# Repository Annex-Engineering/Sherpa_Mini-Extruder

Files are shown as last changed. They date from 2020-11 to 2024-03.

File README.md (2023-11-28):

## Sherpa Mini - Release 2:

This release adds support for Bondtech's RIDGA v2 in addition to numerous tweaks and updates to make the extruder easier to work on and more reliable than ever. 

## Changelog

+ Bondtech RIDGA v2 compatibility (R2 RC1 and newer)
+ Bondtech insert support
+ Stronger and stiffer idler arm
+ Increased clearance between idler arm and core
+ Minor fixes and adjustments in preparation for upcoming upgrades

+ Core housing and rear housing need to be reprinted if upgrading from Release 1
+ Updated idler arms are backwards compatible with Release 1 and Release 2 RC1

## FAQ
For Material Requirements, Print Settings and How to Interpret the file naming structure, please see: "Print_Settings_and_File_Key.txt"

The BOM and Sourcing Guide for this product can be found here: https://docs.google.com/spreadsheets/d/1O3eyVuQ6M4F03MJSDs4Z71_XyNjXL5HFTZr1jsaAtRc/edit?usp=sharing

## Product Info
This is the Sherpa Mini Extruder, a ground up design developed by Anlin and the team at Annex Engineering. It's a dual geared hobbed filament extruder designed for use with any printer. It features a gear driven design to provide torque while being able to be near silent. You must perform your own tuning to get the best results.

A Pinion Equipped Pancake Stepper is required for this Release.

Our discord server can be found here: 

Join me on Discord (https://discord.gg/MzTR3zE)

Please only use GitHub Issues for repo and file related problems. For general design related questions and technical support please visit our Discord server.

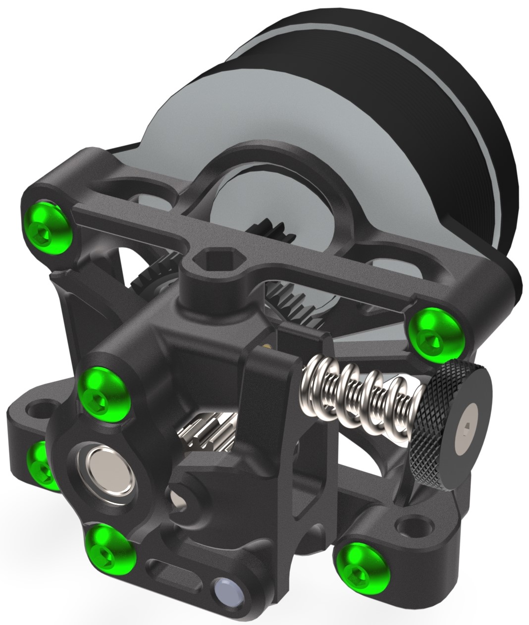
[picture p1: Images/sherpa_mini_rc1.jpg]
Image of Sherpa Extruder


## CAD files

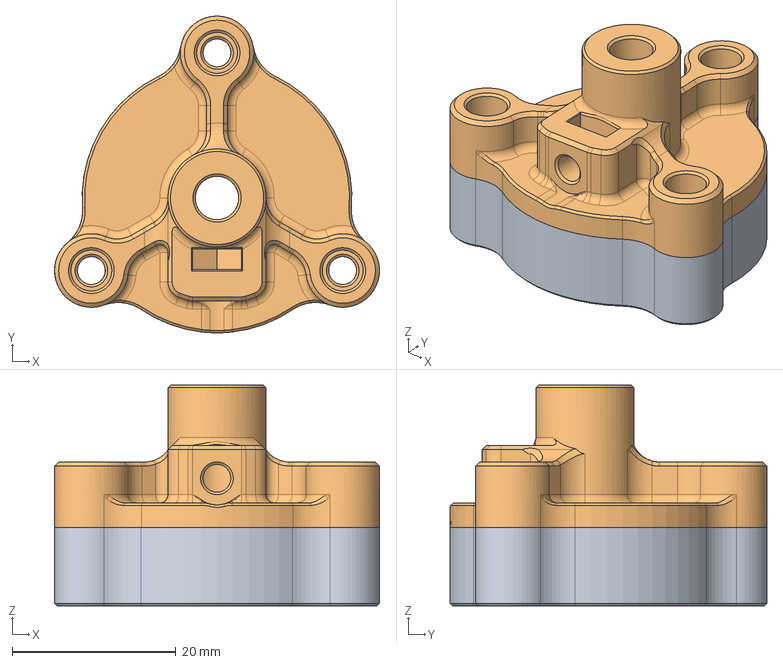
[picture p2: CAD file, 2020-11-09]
Assembly_Tools/Shaft_Grinding_Tool/shaft_block v4.step
39.8 x 38.8 x 27.0 mm
bottom
top

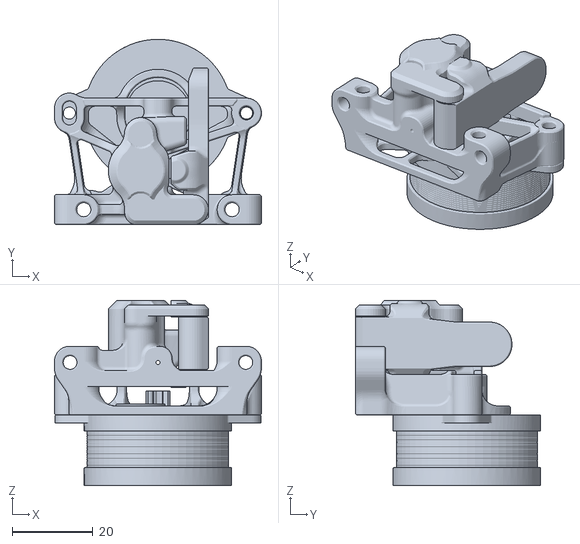
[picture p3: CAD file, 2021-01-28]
Mockup_CAD/sherpa_mini_b3_mockup.STL
51.2 x 45.9 x 45.9

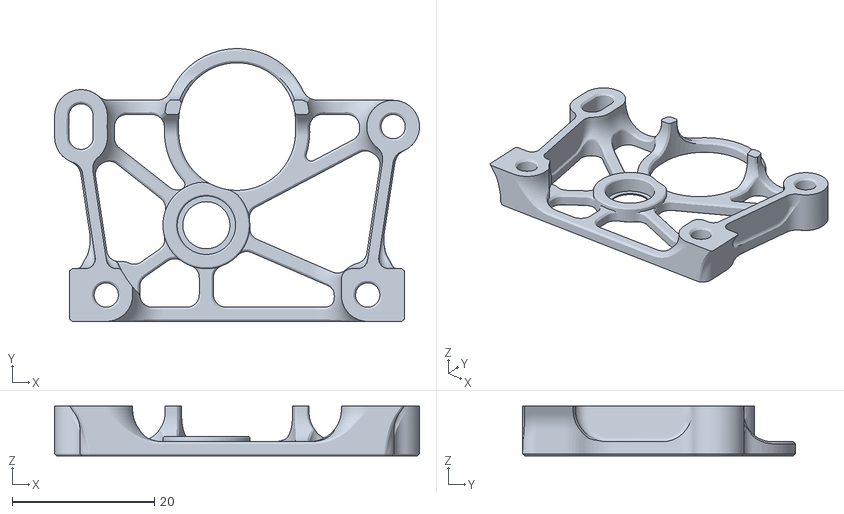
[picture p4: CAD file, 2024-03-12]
STLs/housing_rear_x1_rev17.STL
51.2 x 38.3 x 7.00

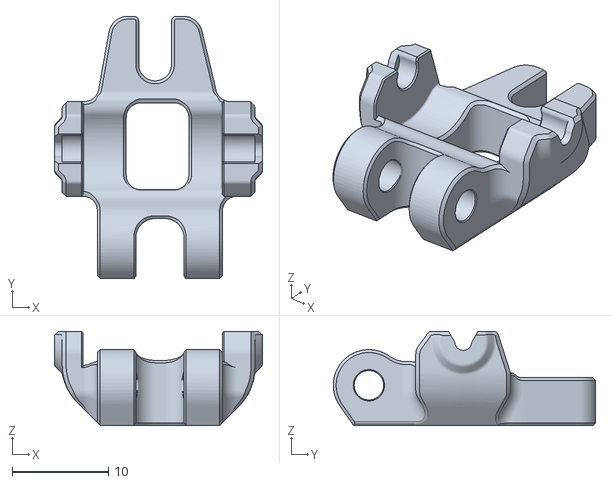
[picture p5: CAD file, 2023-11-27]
STLs/optional_parts/[a]_idler_arm_short_x1_rev16a.STL
21.6 x 27.3 x 9.80

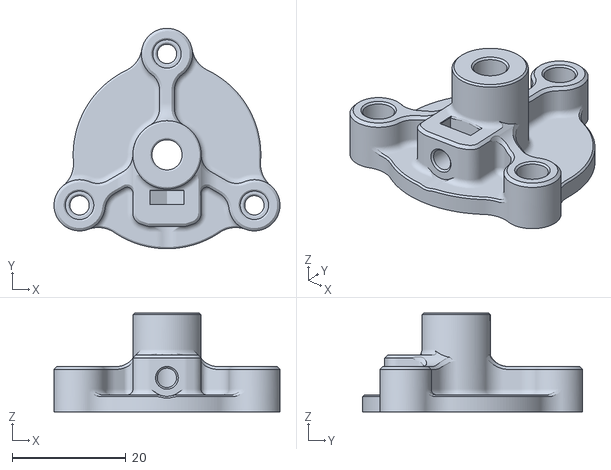
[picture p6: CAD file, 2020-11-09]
Assembly_Tools/Shaft_Grinding_Tool/top.stl
39.7 x 38.8 x 17.4

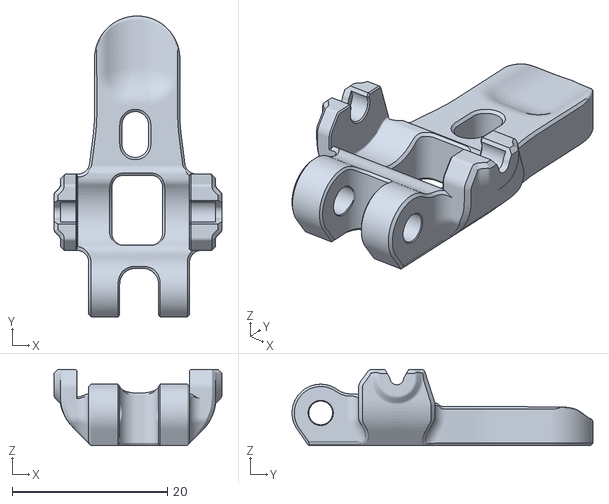
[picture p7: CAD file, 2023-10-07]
STLs/[a]_idler_arm_long_x1_rev16a.STL
21.6 x 38.8 x 9.80

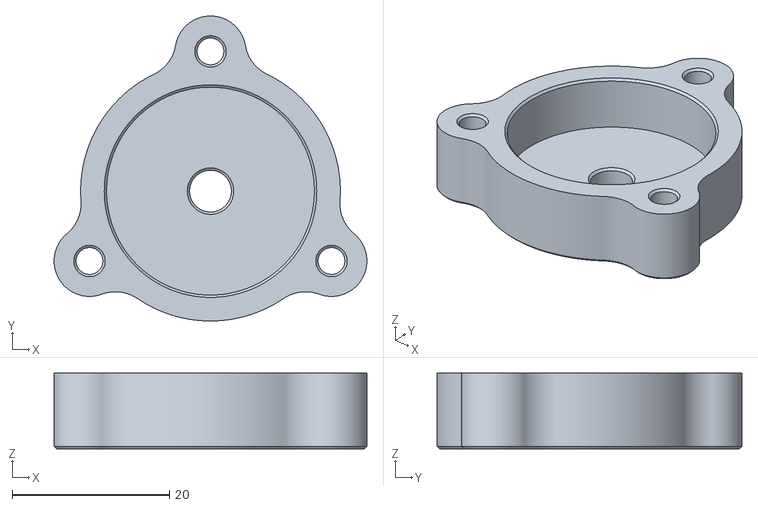
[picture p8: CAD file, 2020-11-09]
Assembly_Tools/Shaft_Grinding_Tool/bottom.stl
39.7 x 38.7 x 9.60

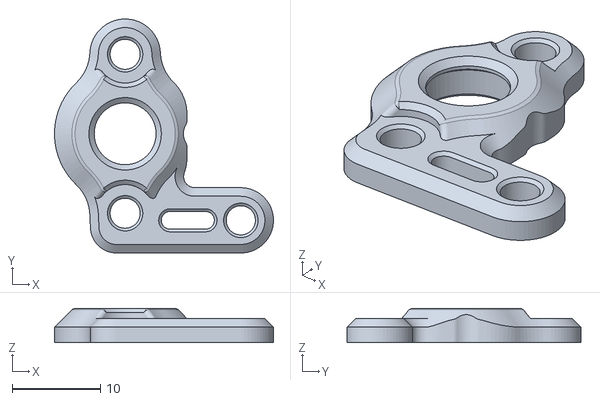
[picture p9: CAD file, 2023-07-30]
STLs/[a]_housing_front_x1_rev15.STL
24.8 x 26.5 x 3.90

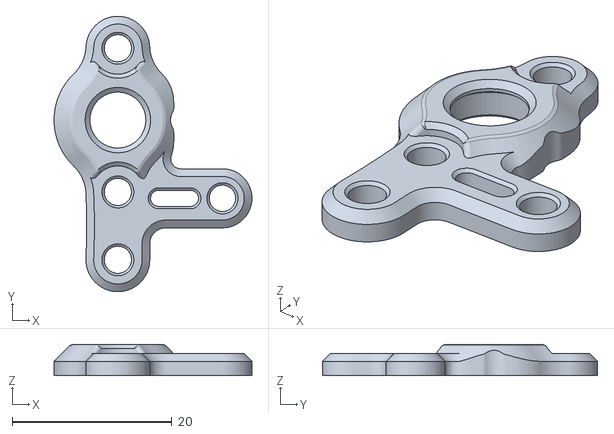
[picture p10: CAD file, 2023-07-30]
STLs/optional_parts/[a]_housing_front_k_x1_rev15.STL
24.8 x 34.5 x 3.90

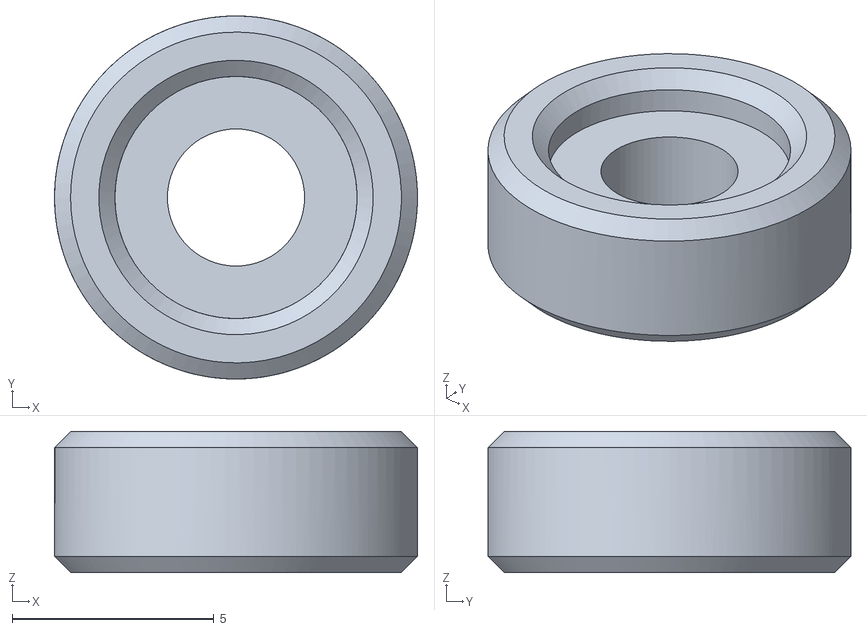
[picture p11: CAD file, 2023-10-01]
STLs/optional_parts/[a]_bondtech_thumbscrew_spacer_x1_rev1.STL
9.00 x 9.00 x 3.50

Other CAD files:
Mockup_CAD/sherpa_mini_b3_mockup.x_t

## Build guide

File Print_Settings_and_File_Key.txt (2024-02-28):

Primary Color: nothing at start of file name
Accent Color: [a]_ at start of file name
Quantity Required: _x# near end of file name
File Revision: _Rev# at end of file name

Nozzle Size: 0.4mm (RECOMMENDED)
Recommended FDM Materials: ASA (Fillamentum, Prusament, Polymaker or 3DXTech Recommended)
Alternate Approved FDM Materials: PC (3DXTech Recommended)
Layer Height: 0.10mm or 0.2mm
Extrusion Width: Forced 0.4mm
Infill Percentage: 40% minimum (at 0.6mm Width)
Infill Type: Grid, Gyroid, Honeycomb, Triangle or Cubic
Wall Count: 4 minimum (at 0.4mm Width)
Solid Top/Bottom Layers: 5 minimum (at 0.2mm Height)

Nozzle Size: 0.5mm 
Recommended FDM Materials: ASA (Fillamentum, Prusament, Polymaker or 3DXTech Recommended)
Alternate Approved FDM Materials: PC (3DXTech Recommended)
Layer Height: 0.1 or 0.2mm
Extrusion Width: Forced 0.5mm
Infill Percentage: 40% minimum (at 0.6mm Width)
Infill Type: Grid, Gyroid, Honeycomb, Triangle or Cubic
Wall Count: 4 minimum (at 0.5mm Width)
Solid Top/Bottom Layers: 5 minimum (at 0.2mm Height)

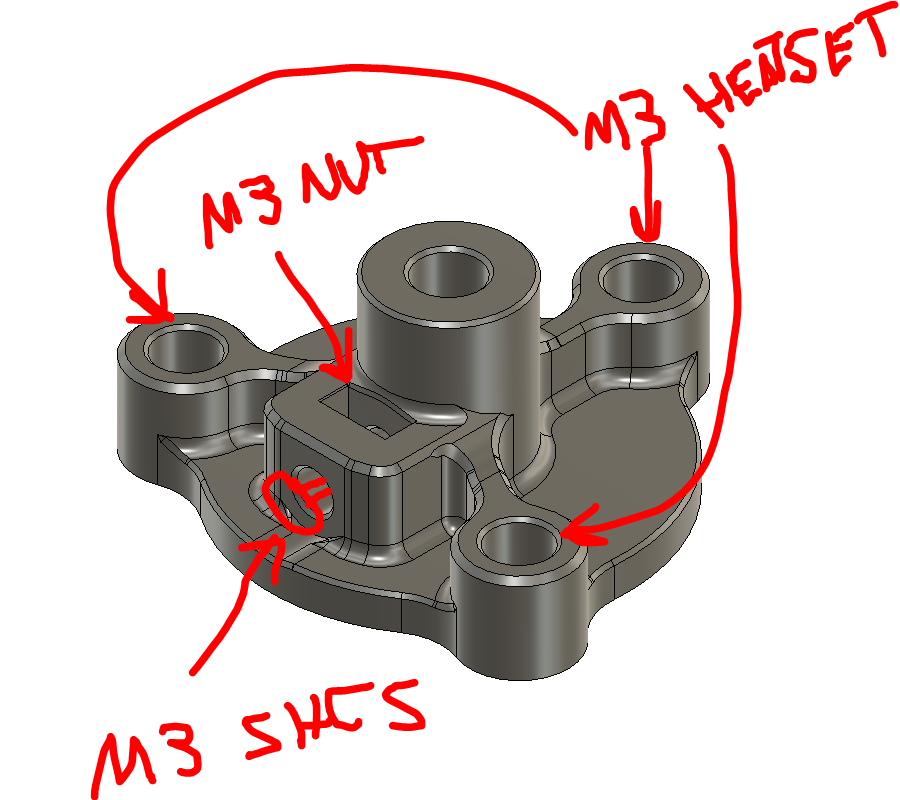
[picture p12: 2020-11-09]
Assembly_Tools/Shaft_Grinding_Tool/tool_2.png

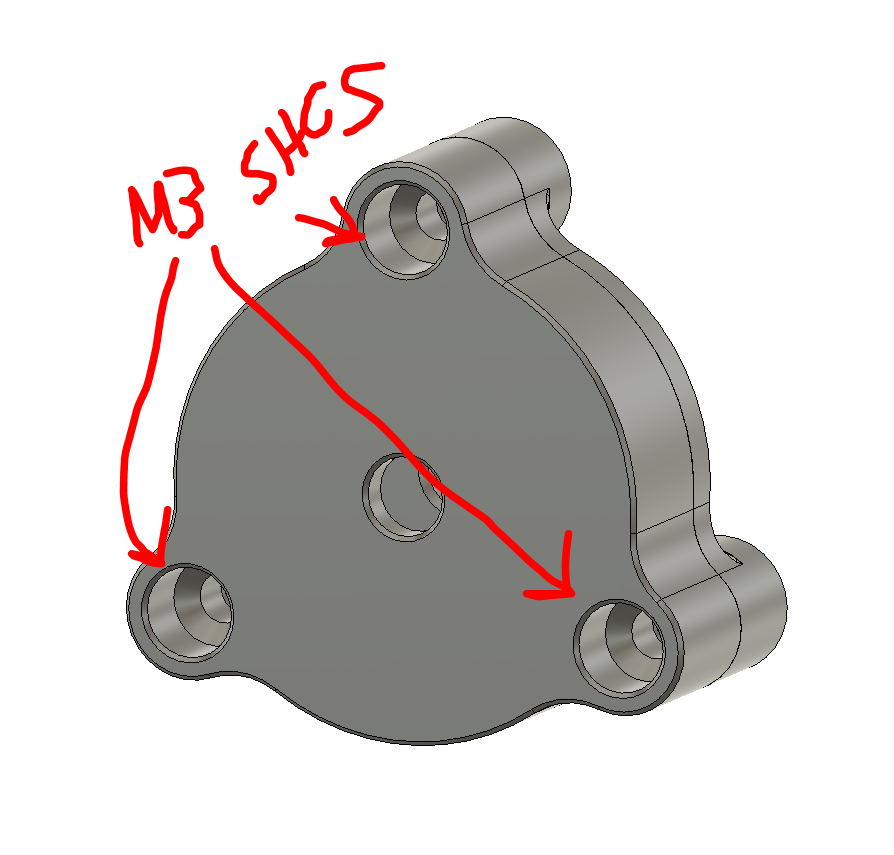
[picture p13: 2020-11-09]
Assembly_Tools/Shaft_Grinding_Tool/tool_1.png

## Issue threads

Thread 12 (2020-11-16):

Step file release.

ChipCE, 2020-11-16:
Hello, thank for very nice design!
Can you guys please release the CAD or STEP file? I need to modify the extruder to use smaller brass Knurled insert.

Annex-Engineering, 2020-11-16:
Steps are only released with non-beta or non-alpha releases.

Closed 2020-11-16.

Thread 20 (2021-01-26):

Holes for mockup

ssavickiy, 2021-01-26:
Hello. I am developing a direct extruder on UltiSteel, but a new mockup cad rc1/beta3 without a pair of lower tightening holes for the screws. My design implies mounting through them on the hotend. These holes will remain in the new release of the stl? And is it possible to add them for mockup cad ?
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

Annex-Engineering, 2021-01-28:
[https://github.com/Annex-Engineering/Sherpa_Mini-Extruder/commit/74c01825e37052597802892bef388b0dc6423901](url)

Closed 2021-01-28.

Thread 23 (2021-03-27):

Teflon tube attachement

Lefuneste83, 2021-03-27:
Hi there. I have been using the Sherpa Mini on my Voron V0 and it is a great design. The only issue I have (and it is a constant pain) is that the bowden tube does not hold in place in the hexagonal hole at the top of the extruder. There is no way I could use glue on a teflon tube. It would not hold to the material. Have you considered a slight modification of this hole to allow for a bowden adapter such as a PC4-M5 or a small clip version. I will try to drill out this hex hole to fit such an adapter but it would be great to provision something for it in the base design.

ChipCE, 2021-03-27:
I agree with @Lefuneste83. Or provide the cad file,it's very hard to deal with the stl with too many curve corners. I can only modify the file in tinkle cad, other softwares I tried failed to map the faces into solid object.

szaghi, 2021-03-27:
Hi all, I have just worked at simple mod using a collet to retain the PTFE tube at the top of the extruder, it is really wip, some modifications are needed (the collet hole is too much small, the collet is too much tight in the current version), I hope to fix it soon, but I can share my simple mod if someone is interested (see pictures attached). It is only a temporary mod until an "official" version with integrated PTFE connector will be available.

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

szaghi, 2021-03-28:
Hi all,

I have fixed some tolerances of my stupid collet-mod, I attach this version below.

Cheers

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
[sherpa-collet-ptfe.zip](https://github.com/Annex-Engineering/Sherpa_Mini-Extruder/files/6217217/sherpa-collet-ptfe.zip)

Annex-Engineering, 2021-03-28:
You guys are welcome to put in a pull request for a user mod. There's a folder on the top level of the directory for this.

Annex-Engineering, 2021-03-30:
user mod has been  added, closing issue

szaghi, 2021-03-30:
Hi all,

I have just created a PR (https://github.com/Annex-Engineering/Sherpa_Mini-Extruder/pull/24) with a *user mod* to provide a version of the housing core with an integrated PTFE retaining collet (see the picture below).

Cheers

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

drewgwallace, 2024-05-12:
I am not finding this adaptation for a PTFE retainer in the user mods - was it removed?

https://github.com/Annex-Engineering/Annex-Engineering_User_Mods/tree/main/Extruders/Sherpa_Mini/Extruder_Mods

Closed 2021-03-30.

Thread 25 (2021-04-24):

collet adapter version has too large hole

5PAZT1C, 2021-04-24:
the hole for the collet adapter as measured is 6.5-6.7mm, for proper fitment with e3d collets the hole needs to be 6mm.

Were the CAD for the modifed version provided, it would be a very easy fix, however the user mod version has no CAD file posted.

5PAZT1C, 2021-04-24:
to further expand on the issue, I have one collet that 'fits' however it is very easy to pop out and the raised lip is also too short, so that even with the retaining clip it wiggles quite a bit. Suggest changing diameter of lip to 6.00mm from it's current ~6.5mm as printed, and increasing the length of the lip by 1.5mm to decrease the amount of play in the collet fitting once retaining clip is inserted.

Alternatively, suggest providing a part number for a collet to be used with this mod, preferably one available from multiple vendors

szaghi, 2021-04-25:
@5PAZT1C

Thank you very much for the insight, I dimensioned the mod with the collet I had (an unknown-manufacturer Chinese one) and with the tolerance of my printer. Now that the CAD file of version 1 has been provided I can re-desing the collet adapter with the dimensions you pointet out. ASAP I will provide the step of my mod with fixed dimensions.

Regards,
Stefano

5PAZT1C, 2021-04-25:
if it helps I found the datasheet for the e3d collet:
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

I would think that making both the inner diameter of the bore and the lip slightly undersized with a taper leading from the inner diameter to the lip would result in a good fitting collet adapter. You can see the documentation for the e3d v6 lite here to see what I mean:

https://wiki.e3d-online.com/images/8/84/DRAWING-LITE6-175-SINK.png

szaghi, 2021-04-25:
@5PAZT1C

This helps a lot, I will use this E3D datasheet as a reference, thank you again.

5PAZT1C, 2021-04-25:
> @5PAZT1C
>
> This helps a lot, I will use this E3D datasheet as a reference, thank you again.

sure thing! Glad I could help contribute, even if it's something small. I'll keep an eye out for the updated version and do a test print, I'll follow up on this once printed

szaghi, 2021-04-25:
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

I hope to find the time tomorrow

5PAZT1C, 2021-04-25:
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

no rush, I have to buy more ABS before I can reprint it anyways lol

Annex-Engineering, 2021-06-19:
seems to be a dead issue, closing for now

szaghi, 2021-06-19:
@Annex-Engineering

Yes, I am sorry, but currently I have not the time to fix it, I hope to find it soon

szaghi, 2021-09-08:
[sherpa-ptfe-collet-retain.zip](https://github.com/Annex-Engineering/Sherpa_Mini-Extruder/files/7131332/sherpa-ptfe-collet-retain.zip)

@5PAZT1C

I am very sorry for my delay, but I was very busy. I have attached a preliminary version of the modified housing with PTFE collet retainer integrated (the whole step and the STL of the modified housing): I designed the collet and housing-collet-retainer using the references you have indicated. Can you give me a feedback (no rush, when you can/want) about it before creating a new PR?

My best regards

5PAZT1C, 2021-09-08:
thanks! I will print it and check fitment when I have time, however it will be quite a while before I can reprint it and check fitment, as I am leaving the country for vacation for a month tommorrow afternoon

szaghi, 2021-09-09:
@5PAZT1C

Do not worry, no rush, enjoy your vacation

Closed 2021-06-19.

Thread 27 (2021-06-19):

VORON0 Retention block missing

mrvanes, 2021-06-19:
The retention block STL is missing in Edward Yeeks VORON0 toolhead.

oldfar-t, 2021-09-08:
It looks like the file was deleted from the v0 Github in april, you can still dig it up through Github search but I've also attached it. It would be nice if it could be put in the STLs folder though.
[[a]_Belt_Retention_Block_x1.zip](https://github.com/Annex-Engineering/Sherpa_Mini-Extruder/files/7125615/a._Belt_Retention_Block_x1.zip)

Closed 2021-09-10.

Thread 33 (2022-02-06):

version with 4.6 inserts

iamkarlson, 2022-02-06:
Is there any technical limitation on why 4.6 mm inserts cannot be used? they seem to be super popular in the Netherlands/Germany and 5mm is almost only can be bought from Chinese shops.

dan-and, 2022-02-08:
Well, there is a 4.6 User-Mod at https://github.com/Annex-Engineering/Sherpa_Mini-Extruder/tree/8163d3f125bbe51e7492368310ab6a8a0761f063/User_Mods which was moved to a new repo with the last commit here.
Maybe check that out or have a look at the sherpa micro project, which may looks like the successor of the sherpa mini.

PapeJelly, 2022-02-24:
Looks like iamkarlson's request has been fulfilled. Therefore i will close this issue.

Closed 2022-02-24.

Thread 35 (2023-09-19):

Wrong STL files?

ogland, 2023-09-19:
I downloaded the latest release files for Sherpa Mini, but what I printed was Sherpa Micro. Are the STLs wrong?

anlin93, 2023-09-24:
Thanks for bringing this to our attention. The issue has now been fixed

Closed 2023-09-24.

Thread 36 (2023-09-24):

Can you make this part more reliable?

pasha4ur, 2023-09-24:
Hello

I printed this part from ABS+ on different printers. It constantly breaks down. I have already replaced 5 parts and 2 sets of gears.

Make it more reliable. Please.

[https://i.ibb.co/XVK9r0Z/photo-2023-09-24-14-00-50.jpg](https://i.ibb.co/XVK9r0Z/photo-2023-09-24-14-00-50.jpg)

anlin93, 2023-09-24:
White ABS is known to be prone to all sorts of problems and is not recommended for structural parts. We very rarely see failures around the idler arm pivot when printed out of ASA (or ABS in almost any other colour). The failure in your case seems to be related to inadequate layer adhesion which can be caused by a number of things, one of them being the material. Overextrusion or badly printed overhangs can also stress the plastic around the pivot, so if the pivot shaft requires more than a firm push against a hard surface to insert, you may need to adjust your print settings and/or ream out the pivot hole. There is not enough detail about the print settings, material or the printer to provide a more comprehensive answer. My suggestion is to try a different material (black ASA preferred) and make sure the print settings are appropriate for the material and your printer. If you require further assistance, feel free to post in #sherpa_help_forum on our Discord server, which is our main support channel.

pasha4ur, 2023-09-24:
I printed it in black too. This is bad design problem.

dan-and, 2023-09-24:
I'm sorry, but I haven't had any problems with the structure. I'm using 5 mini and micros and they never broke. I'm not even using the recommended materials, but an ASA from a spanish manufacturer.

anlin93, 2023-09-24:
Sherpa has been out 3 years and so far there have only been a handful of reports of this issue, basically all of which can be attributed to bad prints. As the problem remains isolated to your case, no design changes are planned. If you want to post your modified file as a mod, feel free to make a pull request. Any further communication should happen on our Discord server, as instructed above. I will add a note to the main repo README that GitHub issues are not a forum for technical support.

Closed 2023-09-24.

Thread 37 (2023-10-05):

Normal cad file

pasha4ur, 2023-10-05:
Hello

Why don't you share stp or other editable file format as Salfin, Orbiter, Vz-HextrudORT, etc?

Edrawings can't be imported in solidworks and other apps. It says about unsupported format.

anlin93, 2023-10-05:
Cad files for the R2 will be released when it reaches final release status. Cad files for R1 are available here: https://github.com/Annex-Engineering/Sherpa_Mini-Extruder/tree/87c5b7f5262ed1ce753bf90fcbf62043f1d25eba/CAD

Closed 2023-10-05.

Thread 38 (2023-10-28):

Sherpa Klipper Config

4e576rt8uh9ij9okp, 2023-10-28:
Hello there, so I have seen links online to this here but sadly someone decided to delete it.
https://github.com/Annex-Engineering/Sherpa_Mini-Extruder/blob/master/Klipper_Config_Block.txt

Now will there be a klipper config for it or does the whole world need to reinvent the wheel (every person needs to find it out)

anlin93, 2023-11-02:
The Klipper config block can be found here:
https://github.com/Annex-Engineering/ANNEX-Printer-Firmware/tree/main/Klipper_and_Klipper_Derivatives/Sherpa_Mini

Closed 2023-11-02.

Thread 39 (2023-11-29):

Little questions about print settings

celtare21, 2023-11-29:
So in the print settings it states as follows:

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

Does that mean that the extrusion width for infill is 0.8 like this?
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

And what does 4 top/bottom laters at 0.5mm **Height** mean more exactly?

Thank you

ChaosBlades, 2024-02-28:
Those settings are for 0.5mm nozzles. Most people have 0.4mm which is after those settings. Don't know why those settings are even listed to be honest. Does not even apply to 99.9% of people. Don't even think that is an exaggeration.

If you have printed Voron parts at Voron recommended settings then you can print this at those same settings. Plenty of guides and information online on how to do that.

celtare21, 2024-02-28:
> Those settings are for 0.5mm nozzles. Most people have 0.4mm which is after those settings. Don't know why those settings are even listed to be honest. Does not even apply to 99.9% of people. Don't even think that is an exaggeration.
>
> If you have printed Voron parts at Voron recommended settings then you can print this at those same settings. Plenty of guides and information online on how to do that.

I actually have a 0.5 mm nozzle 😅.
The bozzle comes standard with 0.5

ChaosBlades, 2024-02-28:
What printer comes standard with 0.5mm? I have literally never heard of anyone using a 0.5mm nozzle. 0.6, 0.8, and even a 1.2mm nozzle but never 0.5mm.

I just looked through every printer profile OrcaSlicer offers and only the Ender 5 Pro and the two VZBots even have profiles for 0.5mm. Which none of those come standard with them.

celtare21, 2024-02-28:
> What printer comes standard with 0.5mm? I have literally never heard of anyone using a 0.5mm nozzle. 0.6, 0.8, and even a 1.2mm nozzle but never 0.5mm.
>
> I just looked through every printer profile OrcaSlicer offers and only the Ender 5 Pro and the two VZBots even have profiles for 0.5mm. Which none of those come standard with them.

None come "standard". I have a fully custom printer, everything was replaced and or modified. I make my own slicer profiles and this is the nozzle I'm using https://northprint3d.ca/product/tungsten-carbide-nozzle-high-flow/

anlin93, 2024-02-28:
Sorry, somehow this issue slipped through the cracks and I only got a notification for it now. The print settings file will probably be removed at some point as the relevant information can be found in the build manual. For now I've updated the print settings file to match our current recommendations.

Closed 2024-02-28.

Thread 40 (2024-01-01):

Release 2 CAD missing idler_arm_long

310weber, 2024-01-01:
The CAD for release 2 seems to be missing the idler_arm_long part (or rather the part shows up in the model tree but is empty).

Steps to reproduce:
1. download parasolid model [sherpa_mini_release_2.x_t](https://github.com/Annex-Engineering/Sherpa_Mini-Extruder/blob/master/CAD/sherpa_mini_release_2.x_t) from commit [fa76f44](https://github.com/Annex-Engineering/Sherpa_Mini-Extruder/commit/fa76f449e86c1e4ee2c25fc557be01597a096812)
2. import model to Onshape
3. navigate to "idler_arm_long^housing_sherpa_mini_a3_r16(FDM)" in the model tree
4. part is empty

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

ChaosBlades, 2024-02-28:
It is not missing... just really really small 🤣 I compared Release 1 and Release 2 arms. The geometry is different so you can't simply split the old thumb lever and add it to the new idler arm short.
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
Also, would be nice when this is fixed it is updated to a Step file instead of the Parasolid file. The ONLY free way a user can use that file is add it to Onshape then export it as a Step. Who knows how long it will be before that is locked behind a pay wall as well.

So people don't have to make an Onshape account to use the current CAD I have already converted it.
[sherpa_mini_release_2.zip](https://github.com/Annex-Engineering/Sherpa_Mini-Extruder/files/14431012/sherpa_mini_release_2.zip)

anlin93, 2024-02-28:
This looks to be an issue related to Onshape. The X_T opens fine in SolidWorks, long idler arm included
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

Closed 2024-02-28.

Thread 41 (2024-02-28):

Release 2 Idler Arm Long collides with idler gear teeth

ChaosBlades, 2024-02-28:
The idler gear teeth hit the long idler arm but not the short. Could be something slightly tweaked on the long version of the arm. Can't tell if there is anything different about them due to https://github.com/Annex-Engineering/Sherpa_Mini-Extruder/issues/40 or if it is a print issue. It does spin free if I put the gear in backwards. The tolerances on both due seem unnecessarily tight or the idler I have just has slightly longer teeth than the one used to design the part.

In CAD the Idler gear is 9.46mm in diameter and mine is 9.54mm and the CAD model gears has 0.25mm of clearance with the arm.

anlin93, 2024-02-28:
Please only use GitHub Issues for repo and file related problems. For general design related questions and technical support please visit our Discord server. That being said both idler arm variants have identical gear clearances, so this is most likely a print issue.

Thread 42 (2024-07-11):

Documentation: Current for LDO Motors and Klipper config

leo-hstone, 2024-07-11:
Hi, first: thanks for the awesome design!

Would it be possible to include the current setting for the motor as well as a starting point for a klipper config in this repo? I would be happy to contribute if guided where to place things.

leo-hstone, 2024-07-11:
Just seen #38 - here is all the information. In this case: please include a link to there in the ReadMe in a highlighted position.

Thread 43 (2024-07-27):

Documentation and/or Assembly Tool: PTFE tube length

wirehead, 2024-07-27:
At least by documenting, potentially by creating an assembly tool cutting jig (there might be one?) can there be documentation for how long the PTFE tube ought to stick into the Sherpa?

I think it's 8mm, but I'm not actually sure.

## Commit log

2020-08-27 sherpa mini stl "pre-release"
    sherpa mini stl "pre-release"
    [1011_china_chain_x_carriage_mount_rev1.stl, 4010_cooling_duct_focussed_left_rev1.stl, 4010_cooling_duct_focussed_right_rev1.stl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]
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2020-08-30 MInor tweaks and updates
    Raise omron probe up for clearance in x carriage, tweaks to focussed cooling duct for better performance. Add igus chain mount.
    [4010_cooling_duct_focussed_left_rev1.stl, 4010_cooling_duct_focussed_left_v2.stl, 4010_cooling_duct_focussed_right_rev1.stl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]
2020-08-31 Multiple updates
    - Tweaked heatset insert hole sizes
    - Add Denali/V1.8 compatible carriage
    - Updated dragon mount with inserts coming in from bottom.
    - Added images and a readme
    [dragon_sherpa_mini_mount_single_unit_rev1.stl, dragon_sherpa_mini_mount_single_unit_rev2.stl, x_carriage_left_mag_microswitch_rev1.stl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]
2020-09-06 Update STLs + config
    [Klipper_Config_Block.txt, [a]_idler_carrier_long_x1_rev1.stl, [a]_idler_carrier_long_x1_rev2.stl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]
2020-09-09 add sherpa mini assembly STL
    [sherpa_mini_assy_a1.stl]
2020-09-11 add edwardyeeks experimental sherpa mini v0 toolhead to the repo
    [cooling_fan_duct_left_v1.stl, cooling_fan_duct_right_v1.stl, dragon_toolhead_left_v1.stl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]
2020-09-11 Fix hole positions in dragon & mosquito toolheads. Updated CAD.
    [dragon_toolhead_left_v1.stl, dragon_toolhead_left_v2.stl, dragon_toolhead_right_v1.stl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]
2020-09-12 Add bridges in cooling fan duct screw holes to avoid printing with supports.
    [cooling_fan_duct_left_v1.stl, cooling_fan_duct_left_v2.stl, cooling_fan_duct_right_v1.stl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]
2020-09-12 Fix weird stl orientation causing non-flat top surfaces.
    [cooling_fan_duct_left_v2.stl, cooling_fan_duct_right_v2.stl]
2020-09-15 Add CAD, update magnetic x carriage stls
    - CAD released for the toolhead and x carriage.
    - magnet holes were adjusted to match current moron magnetic microswitch probe.
    - renamed stls to have revx number.
    [4010_cooling_duct_focussed_left_rev2.stl, 4010_cooling_duct_focussed_left_v2.stl, 4010_cooling_duct_focussed_right_rev2.stl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]
2020-09-20 Updated CAD File
    File was missing omron x-carriage.
2020-09-21 Alpha 2 release
    - Reduce frontage and plastic usage.
    - Better wire routing and more ziptie mounting points.
    - Optimise cooling fan duct to blow closer to nozzle (untested).
    [cooling_fan_duct_focussed_left_a2_v1.stl, cooling_fan_duct_focussed_right_a2_v1.stl, cooling_fan_duct_left_v2.stl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]
2020-10-09 Initial commit of Release 2
    - push cooling blower fans forward by 4mm to allow clearance for V1.8 and V2.4 gantries.
    - move microswitch inwards a little bit for V1.8/Denali x carriage.
    - now only supports 4010 axial fan for hotend
    - now only has the updated focussed cooling duct edition
    [4010_cooling_duct_focussed_left_rev2.stl, 4010_cooling_duct_focussed_left_rev3.stl, 4010_cooling_duct_focussed_right_rev2.stl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]
2020-11-04 add pape toolhead for v6s
    [4010_radial_fanduct_focussed_left.STL, 4010_radial_fanduct_focussed_right.STL, V6_sherpa_mini_mount_back.STL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]
2020-11-08 add xile tiny-m toolhead
    [carriage_left.STL, carriage_right.STL, fanduct_left.STL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]
2020-11-08 add edwardyeeks sherpa mini mosquito parts
    [4010_cooling_duct_focussed_left_rev3.stl, 4010_cooling_duct_focussed_right_rev3.stl, 4010_radial_fanduct_focused_left_rev4.STL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]
2020-11-09 add shaft grinding tool
    [bottom.stl, shaft_block v4.step, top.stl]
2020-11-09 add shaft grind tool assembly photos
    [bottom.stl, shaft_block v4.step, top.stl]
2020-11-09 add printable bondtech 50t gear to repo (optional)
    [printable_sherpa_mini_gear_50t_sl_x1_rev1.stl]
2020-11-30 sherpa mini - beta 2
    [[a]_housing_front_kseries_x1_rev1.STL, [a]_housing_front_x1_rev3.STL, [a]_idler_arm_long_x1_rev3.STL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]
2020-11-30 fix short idler arm, wrong version marked
    [[a]_idler_arm_short_alt_x1_rev3.STL, [a]_idler_arm_short_x1_rev3.STL]
2020-12-02 Sherpa Mini V0 Toolhead Beta 1
    [cooling_fan_duct_focussed_left_a2_v1.stl, cooling_fan_duct_focussed_left_rev1.stl, cooling_fan_duct_focussed_right_a2_v1.stl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]
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2020-12-17 Revert cooling ducts to previous rev
    Rev4 cooling ducts were an error which was actually an older revision. Reverted back to rev3. Readme was also updated. Small folder reorganisation.
    [4010_cooling_duct_focussed_left_rev3.stl, 4010_cooling_duct_focussed_right_rev3.stl, 4010_radial_fanduct_focused_left_rev4.STL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]
2020-12-21 fix print orientation
    [[a]_idler_arm_short_alt_x1_rev3.STL]
2020-12-24 add hartk1213 bowden adapter
    [SherpaBowden.STL, SherpaBowden.step]
2020-12-26 Add support for Voron Legacy
    [Arm_1.STL, Arm_2.STL, Belt_clamp.STL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]
2020-12-30 Add support for V2.4
    [2x Beltclip.STL, Cable chain anchor - Generic.STL, Cable chain anchor - IGUS.STL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]
2021-01-01 Add experimental microprobe dock to V2.4 toolhead
    [Experimental_microprobe_arm_rev1.x_t, Microswitch_dock.STL, Mount.STL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]
2021-01-11 move xy carriages to "other printer mods" repo
    [1011_china_chain_x_carriage_mount_rev1.stl, 2x Beltclip.STL, 4010_cooling_duct_focussed_left_rev3.stl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]
2021-01-23 add rc1/beta3 better mockup cad to repo (stls coming soon), actual cad to come with RC1
    [sherpa_mini_assy_a1.stl, sherpa_mini_b2_bottom_profile.DXF, sherpa_mini_b3_mockup.SLDPRT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]
2021-01-28 add front holes to mockup model
    [sherpa_mini_b3_mockup.SLDPRT, sherpa_mini_b3_mockup.STL, sherpa_mini_b3_mockup.x_t]
2021-02-07 update block to rotation distance
    [Klipper_Config_Block.txt]
2021-02-09 Update left cooling duct
    Slightly optimised duct for more even airflow on the left side
    [cooling_fan_duct_focussed_left_rev1.stl, cooling_fan_duct_focussed_left_rev2.stl]
2021-02-25 add k-series bolt down to mockup
    [sherpa_mini_b3_mockup.SLDPRT]
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2021-03-26 added stls
    added stls for the 4.6mm OD insert
    [housing_front.STL, housing_front_k.STL, housing_rear.STL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]
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2021-03-27 move optional parts to optional parts folder
    [[a]_housing_front_kseries_x1_rev2.STL, [a]_idler_arm_short_x1_rev4.STL, printable_sherpa_mini_gear_50t_sl_x1_rev1.stl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]
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2021-03-30 User Mod: housing with integrated PTFE Collet
    Short description:
    Add a new housing core version with integrated PTFE retaining collet for
    a more simple PTFE tube handling. To work it requires additional
    materials, i.e. an E3D like collet and clip.
    This modification has been made from the revision 4.
    Why:
    Make more simple the handling of PTFE tube at the inlet of the extruder.
    This change addresses the need by:
    Add a new mesh of the housing core part.
    Side effects:
    Nothing, but it has not been tested yet.
    Note:
    A minor typo has been fixed into *User_Mods/Readme.md* file.
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2021-04-15 add 8t block for gear ratio, made standard
    [Klipper_Config_Block.txt]
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2021-04-21 add highly experimental stls for SLS and MJF printing
    this does not mean we support parts printed from sls or MJF, these parts exist so we can work with external vendors, test parts, and get properly fitting components
    [[a]_housing_front_k_x1_rev5.STL, [a]_housing_front_x1_rev5.STL, [a]_idler_arm_long_x1_rev5.STL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]
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2021-09-24 Updated to R1 parts
    Past parts were RC1 and these are currently R1.
    [housing_front.STL, housing_front_k.STL, housing_rear.STL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]
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2023-07-30 add correct stls to repo
    [[a]_housing_front_k_x1_rev15.STL, [a]_housing_front_k_x1_rev7.STL, [a]_housing_front_x1_rev15.STL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]
2023-10-07 fixed export of stl, reprint recommended
    [[a]_idler_arm_long_x1_rev16.STL, [a]_idler_arm_long_x1_rev16a.STL]
2023-10-27 migrate printer, extruder and board configs to an MIT licensed repo
    [Klipper_Config_Block.txt]
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2023-12-02 CAD fix
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2024-02-28 Update Print_Settings_and_File_Key.txt
    Fix print settings
2024-03-12 Release 2 rev1
    - Reduced rear housing spacer ring thickness (fixes RIDGA alignment)
    - CAD in STEP format
    [housing_rear_bondtech_inserts_x1_rev16.STL, housing_rear_x1_rev16.STL, housing_rear_x1_rev17.STL]
